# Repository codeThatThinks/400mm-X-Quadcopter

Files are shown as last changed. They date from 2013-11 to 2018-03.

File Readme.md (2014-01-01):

## Quadcopter

Drawings, Schematics, Firmware for a quadcopter platform based on APM

## License

The MIT License (MIT)

Copyright (c) 2014 Ian Glen

Permission is hereby granted, free of charge, to any person obtaining a copy of this software and associated documentation files (the "Software"), to deal in the Software without restriction, including without limitation the rights to use, copy, modify, merge, publish, distribute, sublicense, and/or sell copies of the Software, and to permit persons to whom the Software is furnished to do so, subject to the following conditions:

The above copyright notice and this permission notice shall be included in all copies or substantial portions of the Software.

THE SOFTWARE IS PROVIDED "AS IS", WITHOUT WARRANTY OF ANY KIND, EXPRESS OR IMPLIED, INCLUDING BUT NOT LIMITED TO THE WARRANTIES OF MERCHANTABILITY, FITNESS FOR A PARTICULAR PURPOSE AND NONINFRINGEMENT. IN NO EVENT SHALL THE AUTHORS OR COPYRIGHT HOLDERS BE LIABLE FOR ANY CLAIM, DAMAGES OR OTHER LIABILITY, WHETHER IN AN ACTION OF CONTRACT, TORT OR OTHERWISE, ARISING FROM, OUT OF OR IN CONNECTION WITH THE SOFTWARE OR THE USE OR OTHER DEALINGS IN THE SOFTWARE.

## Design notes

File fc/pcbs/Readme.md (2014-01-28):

## Control Board PCB

Control Board

An APM-compatible quadcopter autopilot board. Features an ATSAM4E16C ARM microcontroller, nRF24L01+ RF module, 10DOF IMU module, microSD card, 3.3v switching regulator, 3 SPI, 1 CAN, 1 UART, external navigation lights, an external temperature sensor, and 12 general purpose IO pins.

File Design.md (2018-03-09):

## Design
### Control Board
- APM-based board

- ATSAM3U2C-AU 32-bit Atmel ARM microcontroller
    - external crystal for clocking
    - firmware based on APM, FreeRTOS, ROS, or MultiWii
    - SRAM: run time data (APM: 8k)
    - Flash: firmware (APM: 256k)
    - EEPROM: configuration read from sd card (APM: 4k)
    - SPI (APM: 5)
    - I2C (APM: 1)
    - UART (APM: 4)
    - PWM (APM: 15)
    - external bus interface, for extending memory (APM: no)
    - APM: $17

- microSD card
    - external APM modules
    - configuration
    - data logger

- arming buzzer

- power
    - on/off switch
    - usb connector for external power
    - battery connector
    - connectors for 3.3v rail
    
    - switching power supply, 3.3v
        - provides 3v rail
        - powers all control electronics

    - battery voltage sensor through ADC
    - temp header for battery temp sensor
    - 20V resettable fuse

- connections
    - I2C (2)
    - SPI (1)
    - various ISPs/JTAGs/serials
    - misc I/O pins (analog, digital, PWM)

    - 4x 6-pin right-angle arm headers
        - ESC power (2 pins)
        - misc power (1 pin)
        - ground (1 pin)
        - empty (2 pin)

- LEDs
    - blue power LED
    - red/green arming status LED

    - nav LEDs:
        - 4x high power white strobe LEDs on rotor tips
        - green nav LED on front right rotor
        - red nav LED on front left rotor
        - 2x red strobe LEDs on bottom front and top back

### IMU
- connects via I2C to control board

- 9-axis board
    - gyro
    - accelrometer
    - altimeter/barometer/pressure sensor
    - sensor fusion

### RF
- nRF24L01+?
- full duplex RF
- Serial PPM

### Motors, Propellers, ESCs
- Turnigy D2830-11 1000kv motors
- APC 8x4 propellers
- Turnigy Multistar 30A ESCs (OPTO)
    - no BEC
    - reflash with SimonK firmware with Arduino

### Frame
- 15 7/16" x 1/4" extruded plastic tube

### Battery

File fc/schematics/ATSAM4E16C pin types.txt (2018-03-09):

Power Supplies
5 - VDDIN
19 - VDDIO
28 - VDDIO
68 - VDDIO
93 - VDDIO

4 - VDDOUT
18 - VDDCORE
22 - VDDCORE
86 - VDDCORE
96 - VDDPLL

3 - GND
6 - GND
7 - GND
8 - GND
10 - GND
29 - GND
67 - GND

Clocks, Oscillators, PLLs
24 - XIN32
25 - XOUT32
99 - XIN
98 - XOUT

81 - PCK0
100 - PCK0
16 - PCK1
21 - PCK1
15 - PCK2
20 - PCK2
83 - PCK2

real-time clock
12 - RTCOUT0
11 - RTCOUT1

SWD/JTAG
57 - TMS/SWDIO
63 - TCK/SWCLK
73 - JTAGSEL
74 - TDI
77 - TDO/TRACESWO

Flash
61 - ERASE

Reset/Test
58 - NRST
60 - TST

UART
46 - UTXD0
54 - URXD0
81 - UTXD1
52 - URXD1

PIOA
72 - PA0
70 - PA1
66 - PA2
64 - PA3
55 - PA4
52 - PA5
81 - PA6
24 - PA7
25 - PA8
54 - PA9
46 - PA10
44 - PA11
48 - PA12
27 - PA13
34 - PA14
33 - PA15
30 - PA16
16 - PA17
15 - PA18
14 - PA19
13 - PA20
21 - PA21
26 - PA22
31 - PA23
38 - PA24
40 - PA25
42 - PA26
50 - PA27
79 - PA28
90 - PA29
82 - PA30
83 - PA31

PIOB
12 - PB0
11 - PB1
17 - PB2
20 - PB3
74 - PB4
77 - PB5
57 - PB6
63 - PB7
98 - PB8
99 - PB9
94 - PB10
95 - PB11
61 - PB12
100 - PB13
97 - PB14

PIOD
1 - PD0
92 - PD1
91 - PD2
89 - PD3
88 - PD4
87 - PD5
85 - PD6
84 - PD7
80 - PD8
78 - PD9
71 - PD10
69 - PD11
65 - PD12
62 - PD13
59 - PD14
75 - PD15
56 - PD16
53 - PD17
49 - PD18
47 - PD19
45 - PD20
43 - PD21
41 - PD22
39 - PD23
37 - PD24
35 - PD25
36 - PD26
32 - PD27
51 - PD28
76 - PD29
23 - PD30
2 - PD31

PIO Parallel Capture Mode
31 - PIODCCLK
33 - PIODCEN1
30 - PIODCEN2
38 - PIODC0
40 - PIODC1
42 - PIODC2
50 - PIODC3
79 - PIODC4
90 - PIODC5
82 - PIODC6
83 - PIODC7

SD Card
90 - MCCK
79 - MCCDA
82 - MCDA0
83 - MCDA1
42 - MCDA2
50 - MCDA3

USART
100 - SCK0
11 - TXD0
12 - RXD0
20 - RTS0
17 - CTS0

31 - SCK1
26 - TXD1
21 - RXD1
38 - RTS1
40 - CTS1
50 - DTR1
79 - DSR1
42 - DCD1
90 - RI1

Timer/Counter
72 - TIOA0
70 - TIOB0
55 - TCLK0
33 - TIOA1
30 - TIOB1
79 - TCLK1
42 - TIOA2
50 - TIOB2
90 - TCLK2

SPI
48 - MISO
27 - MOSI
34 - SPCK

44 - NPCS0
54 - NPCS1
83 - NPCS1
97 - NPCS1
17 - NPCS2
46 - NPCS2
82 - NPCS2
26 - NPCS3
52 - NPCS3
64 - NPCS3

I2C
64 - TWD0
55 - TWCK0
74 - TWD1
77 - TWCK1

Analog
9 - ADVREF

12-bit AFE
25 - AFE0_ADTRG
16 - AFE0_AD0
15 - AFE0_AD1
14 - AFE0_AD2
13 - AFE0_AD3
12 - AFE0_AD4
11 - AFE0_AD5
17 - AFE1_AD0
20 - AFE1_AD1
21 - AFE1_AD2
26 - AFE1_AD3

12-bit DAC
66 - DATRG
100 - DAC0
97 - DAC1

FFPI
55 - PGMN0
52 - PGMN1
81 - PGMN2
24 - PGMN3

25 - PGMD0
54 - PGMD1
46 - PGMD2
44 - PGMD3
48 - PGMD4
27 - PGMD5
34 - PGMD6
33 - PGMD7
30 - PGMD8
16 - PGMD9
15 - PGMD10
14 - PGMD11
13 - PGMD12
21 - PGMD13
26 - PGMD14
31 - PGMD15

70 - PGMRDY
64 - PGMNVALID
66 - PGMNOE

PWM
54 - PWMFI0

12 - PWMH0
31 - PWMH0
44 - PWMH0
45 - PWMH0
72 - PWMH0
14 - PWML0
37 - PWML0
77 - PWML0

11 - PWMH1
38 - PWMH1
43 - PWMH1
48 - PWMH1
70 - PWMH1
13 - PWML1
35 - PWML1
61 - PWML1

27 - PWMH2
40 - PWMH2
41 - PWMH2
66 - PWMH2
74 - PWMH2
30 - PWML2
36 - PWML2
82 - PWML2
100 - PWML2

16 - PWMH3
24 - PWMH3
34 - PWMH3
39 - PWMH3
97 - PWMH3
32 - PWML3
33 - PWML3

Ethernet
1 - GREFCK
1 - GTXCK
59 - GRXCK
92 - GTXEN
91 - GTX0
89 - GTX1
75 - GTX2
56 - GTX3
53 - GTXER
88 - GRXDV
87 - GRX0
85 - GRX1
69 - GRX2
65 - GRX3
84 - GRXER
71 - GCRS
88 - GCRSDV
62 - GCOL
80 - GMDC
78 - GMDIO

CAN
17 - CANTX0
20 - CANRX0

USB
94 - DDM
95 - DDP

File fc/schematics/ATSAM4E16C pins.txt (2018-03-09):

1 PD0
2 PD31
3 GND
4 VDDOUT
5 VDDIN
6 GND
7 GND
8 GND
9 ADVREF
10 GND
11 PB1
12 PB0
13 PA20/PGMD12
14 PA19/PGMD11
15 PA18/PGMD10
16 PA17/PGMD9
17 PB2
18 VDDCORE
19 VDDIO
20 PB3
21 PA21/PGMD13
22 VDDCORE
23 PD30
24 PA7/PGMN3
25 PA8/PGMD0
26 PA22/PGMD14
27 PA13/PGMD5
28 VDDIO
29 GND
30 PA16/PGMD8
31 PA23/PGMD15
32 PD27
33 PA15/PGMD7
34 PA14/PGMD6
35 PD25
36 PD26
37 PD24
38 PA24
39 PD23
40 PA25
41 PD22
42 PA26
43 PD21
44 PA11/PGMD3
45 PD20
46 PA10/PGMD2
47 PD19
48 PA12/PGMD4
49 PD18
50 PA27
51 PD28
52 PA5/PGMN1
53 PD17
54 PA9/PGMD1
55 PA4/PGMN0
56 PD16
57 PB6
58 NRST
59 PD14
60 TST
61 PB12
62 PD13
63 PB7
64 PA3/PGMNVALID
65 PD12
66 PA2/PGMNOE
67 GND
68 VDDIO
69 PD11
70 PA1/PGMRDY
71 PD10
72 PA0
73 JTAGSEL
74 PB4
75 PD15
76 PD29
77 PB5
78 PD9
79 PA28
80 PD8
81 PA6/PGMN2
82 PA30
83 PA31
84 PD7
85 PD6
86 VDDCORE
87 PD5
88 PD4
89 PD3
90 PA29
91 PD2
92 PD1
93 VDDIO
94 PB10
95 PB11
96 VDDPLL
97 PB14
98 PB8
99 PB9
100 PB13

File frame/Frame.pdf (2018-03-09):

## PROJECT TITLE

MONTH, DD YYYY

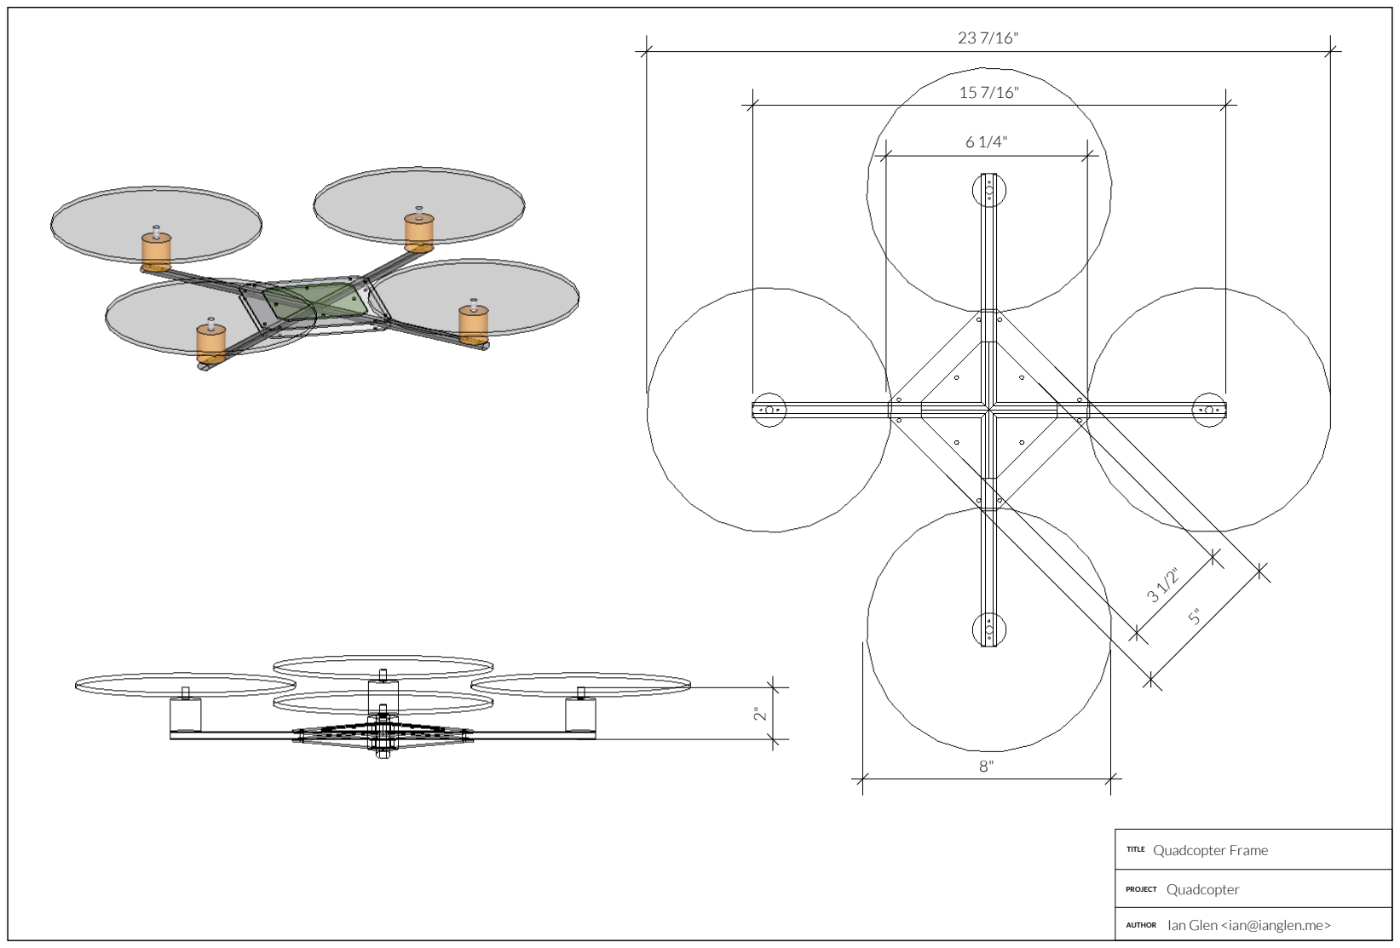
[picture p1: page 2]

TITLE

PROJECT

AUTHOR

Quadcopter Frame

Quadcopter

Ian Glen <ian@ianglen.me>

23 7/16"

15 7/16"

3 1/2"

5"

8"

6 1/4"

2"

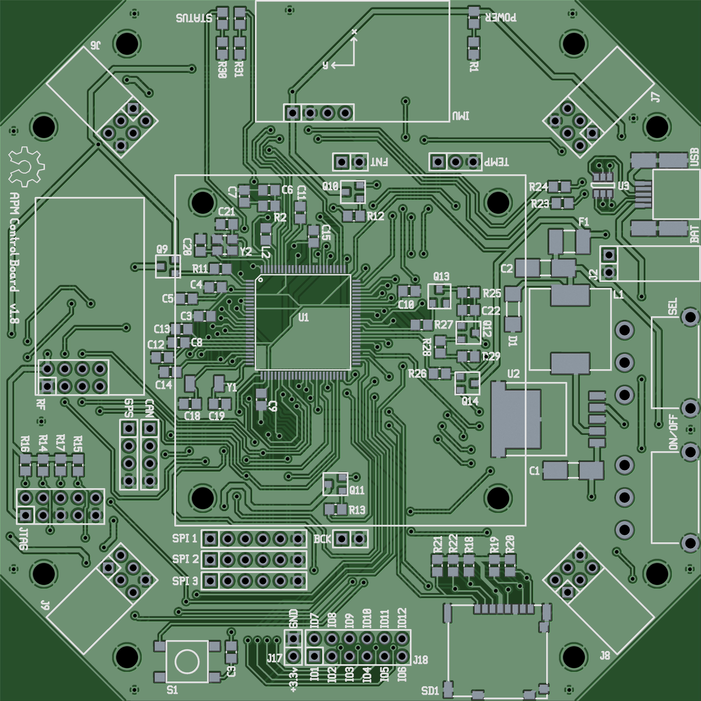
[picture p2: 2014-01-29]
fc/pcbs/Control Board.png

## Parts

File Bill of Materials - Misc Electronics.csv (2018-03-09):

Quantity | Item | URL | Unit Price | Price
4 | 1300mcd white led | http://www.mouser.com/ProductDetail/Kingbright/AA2214VR4D1S-C1/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 | $1.00 | $4.00
4 | 1R 0805 resistor

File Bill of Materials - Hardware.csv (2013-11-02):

Quantity | Item | URL | Cost
4 | Turnigy D2830-11 1000kv motor | http://www.hobbyking.com/hobbyking/store/__28115__D2830_11_1000kv_Brushless_Motor_USA_Warehouse_.html | $39.88
4 | Turnigy Multistar 30A ESC (OPTO) | http://www.hobbyking.com/hobbyking/store/__27776__Turnigy_Multistar_30_Amp_Multi_rotor_Brushless_ESC_2_4S_OPTO_.html | $44.60
1 | APC 8x4 CW propeller (2 pack) | http://hobbyking.com/hobbyking/store/__22971__APC_Style_Propeller_8x4R_Right_Hand_Rotation_2pc_.html | $1.79
1 | APC 8x4 CCW propeller (2 pack) | http://hobbyking.com/hobbyking/store/__22425__APC_Style_Propeller_8x4_2_pc_.html | $2.02
1 | Zippy 4000mAh 3S 25C Lipo | http://hobbyking.com/hobbyking/store/__21360__ZIPPY_Compact_4000mAh_3S_25C_Lipo_Pack.html | $22.30
 |  |  | Total: $110.59

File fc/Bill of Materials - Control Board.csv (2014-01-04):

Quantity | References | Item | URL | Unit Price | Price
ICs
1 | U1 | ATSAM4E16CA-AU | http://www.digikey.com/short/qrd10 | $11.09 | $11.09
1 | U2 | LM2596S-3.3/NOPB | http://www.digikey.com/short/qr0cr | $4.54 | $4.54
1 | U3 | IP4234CZ6-125 | http://www.digikey.com/short/qr077 | $0.46 | $0.46
Inductors
1 | L1 | 100uH inductor | http://www.digikey.com/short/qr07p | $4.42 | $4.42
1 | L2 | 10uH 0805 inductor | http://www.digikey.com/short/qr07r | $0.08 | $0.08
Capacitors
1 | C1 | 100uF low ESR capacitor | http://www.digikey.com/short/qr070 | $1.49 | $1.49
1 | C2 | 470uF low ESR capacitor | http://www.digikey.com/short/qr0tq | $2.46 | $2.46
2 | C3 C12 | 10uF 0805 capacitor | http://www.digikey.com/short/qr0t4 | $0.16 | $0.32
1 | C4 | 2.2uF 0805 capacitor | http://www.digikey.com/short/qr0tf | $0.12 | $0.12
11 | C5-C6 C8-C11 C13-17 | 100nF 0805 capacitor | http://www.digikey.com/short/qr0t1 | $0.03 | $0.34
1 | C7 | 4.7uF 0805 capacitor | http://www.digikey.com/short/qr034 | $0.10 | $0.10
2 | C18-C19 | 22pF 0805 capacitor | http://www.digikey.com/short/qr035 | $0.10 | $0.20
2 | C20-C21 | 1pF 0805 capacitor | http://www.digikey.com/short/qr0q7 | $0.11 | $0.22
1 | C22 | 100pF 0805 capacitor | http://www.digikey.com/short/qr0qp | $0.10 | $0.10
Diodes
1 | D1 | SK32 3A schotty diode | http://www.digikey.com/short/qr0qb | $0.57 | $0.57
1 | LED_PWR | 0805 blue led | http://www.digikey.com/short/qr0q0 | $0.51 | $0.51
1 | LED_ARED | 0805 red led | http://www.digikey.com/short/qr083 | $0.19 | $0.19
1 | LED_AGRN | 0805 green led | http://www.digikey.com/short/qr08m | $0.23 | $0.23
Resistors
2 | R1-R2 | 1R 0805 resistor | http://www.digikey.com/short/qr08f | $0.04 | $0.08
11 | R3-R13 | 300K 0805 resistor | http://www.digikey.com/short/qr0jc | $0.02 | $0.21
5 | R14-R17 R25 | 100K 0805 resistor | http://www.digikey.com/short/qr0jp | $0.04 | $0.20
5 | R18-R22 | 47K 0805 resistor | http://www.digikey.com/short/qr0j2 | $0.04 | $0.20
2 | R23-R24 | 27R 0805 resistor | http://www.digikey.com/short/qr0j1 | $0.10 | $0.20
2 | R26-R27 | 2K 0805 resistor | http://www.digikey.com/short/qr0p2 | $0.04 | $0.08
1 | R28 | 680R 0805 resistor | http://www.digikey.com/short/qr0z8 | $0.04 | $0.04
1 | R29 | 270R 0805 resistor | http://www.digikey.com/short/qr0zh | $0.04 | $0.04
1 | R30 | 75R 0805 resistor | http://www.digikey.com/short/qr0zd | $0.04 | $0.04
1 | R31 | 60R4 0805 resistor | http://www.digikey.com/short/qr04t | $0.04 | $0.04
Transistors
11 | Q1-Q11 | PBMTA14-215 SOT23 | http://www.digikey.com/short/qr04r | $0.36 | $3.96
1 | Q12 | NTR0202PL SOT23 | http://www.digikey.com/short/qr0m3 | $0.52 | $0.52
2 | Q13-Q14 | BC817 SOT23 | http://www.digikey.com/short/qr0mr | $0.21 | $0.42
Switches
2 | PWR PWR_SEL | STDP 5A slide switch | http://www.digikey.com/short/qr0h4 | $2.93 | $5.86
Crystals
1 | Y1 | 32.768KHz crystal | http://www.digikey.com/short/qr0hn | $0.82 | $0.82
1 | Y2 | 12MHz crystal | http://www.digikey.com/short/qr09t | $0.90 | $0.90
Headers
1 | J1 | 2x5 male shrouded | http://www.digikey.com/short/qr09p | $0.26 | $0.26
1 | J2 | 1x2 male right-angle | http://www.digikey.com/short/qr09r | $0.52 | $0.52
1 | J3 | 2x4 female | http://www.digikey.com/short/qr09d | $0.84 | $0.84
33 | J4-J5 J10-J15 | 1x33 male breakaway | http://www.digikey.com/short/qr0b4 | $0.11 | $3.91
4 | J6-J9 | 2x3 male right-angle | http://www.digikey.com/short/qr0bf | $1.07 | $4.28
1 | J16 | 1x4 female | http://www.digikey.com/short/qr05t | $0.60 | $0.60
Misc
1 | F1 | Resettable PTC Fuse 3A | http://www.digikey.com/short/qr05d | $0.15 | $0.15
1 | USB1 | Mini USB AB socket | http://www.digikey.com/short/qr0rz | $2.92 | $2.92
1 | SD1 | Micro SD socket | http://www.digikey.com/short/qr0r9 | $1.84 | $1.84
 |  |  |  | Total: | $56.37

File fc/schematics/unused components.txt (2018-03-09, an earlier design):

unused components
===============================
C12 - 10uF 0805 capacitor
C16 - 100nF 0805 capacitor
C17 - 100nF 0805 capacitor

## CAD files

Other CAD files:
frame/quadcopter.stp
frame/Frame-hidden.skp
frame/Frame.skp

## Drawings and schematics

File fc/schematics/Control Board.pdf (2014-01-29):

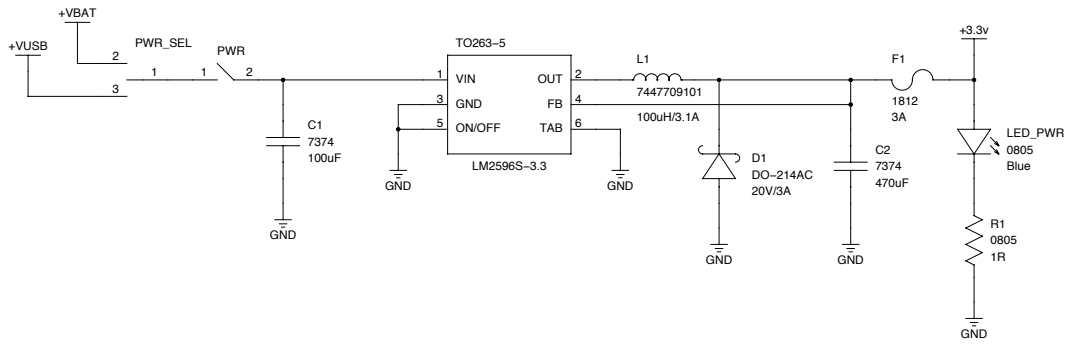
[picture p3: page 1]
DRAWN BY:; PROJECT:; TITLE:; Power; ON/OFF; GND; VIN; 6 TAB; 2 OUT; +VBAT; +VUSB; PWR_SEL; PWR; LED_PWR; Blue

Quadcopter Control Board

Ian Glen <ian@ianglen.me>

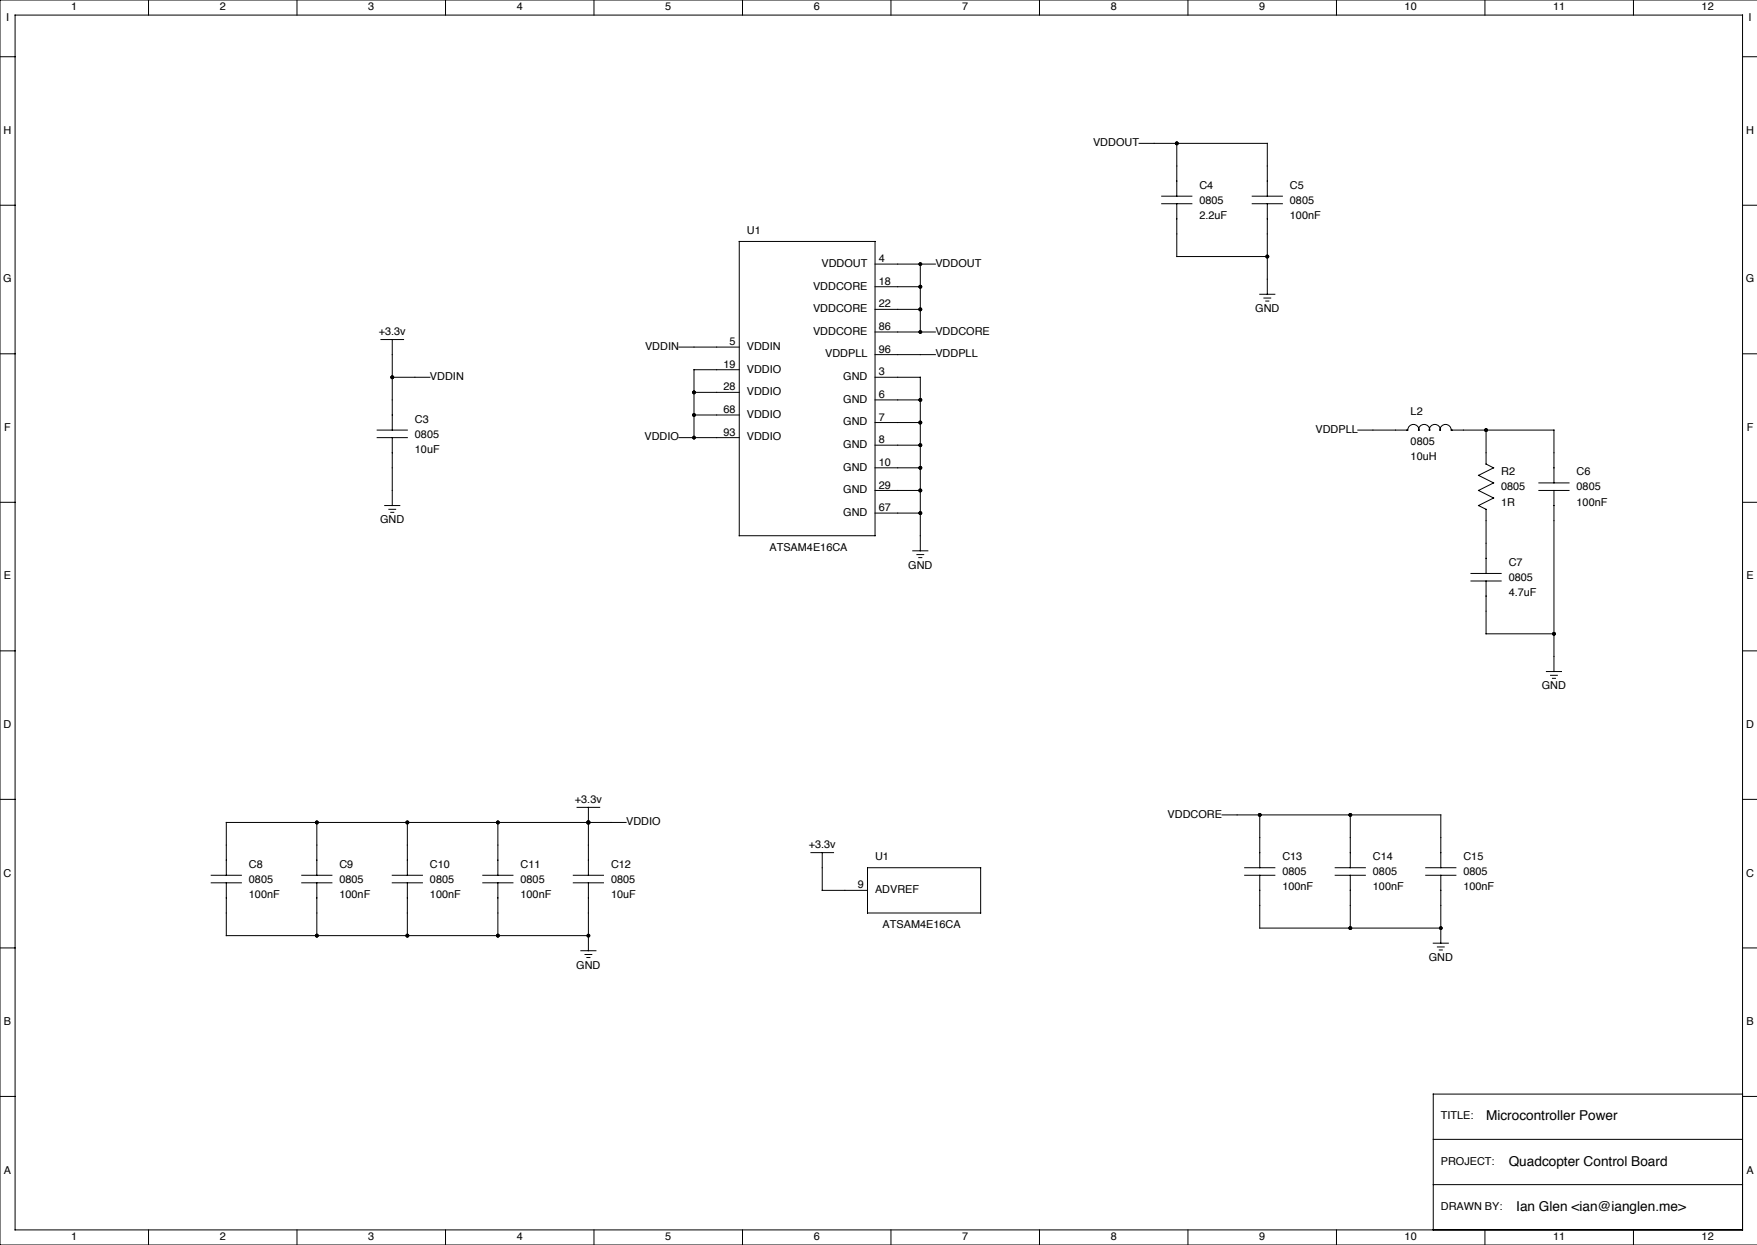
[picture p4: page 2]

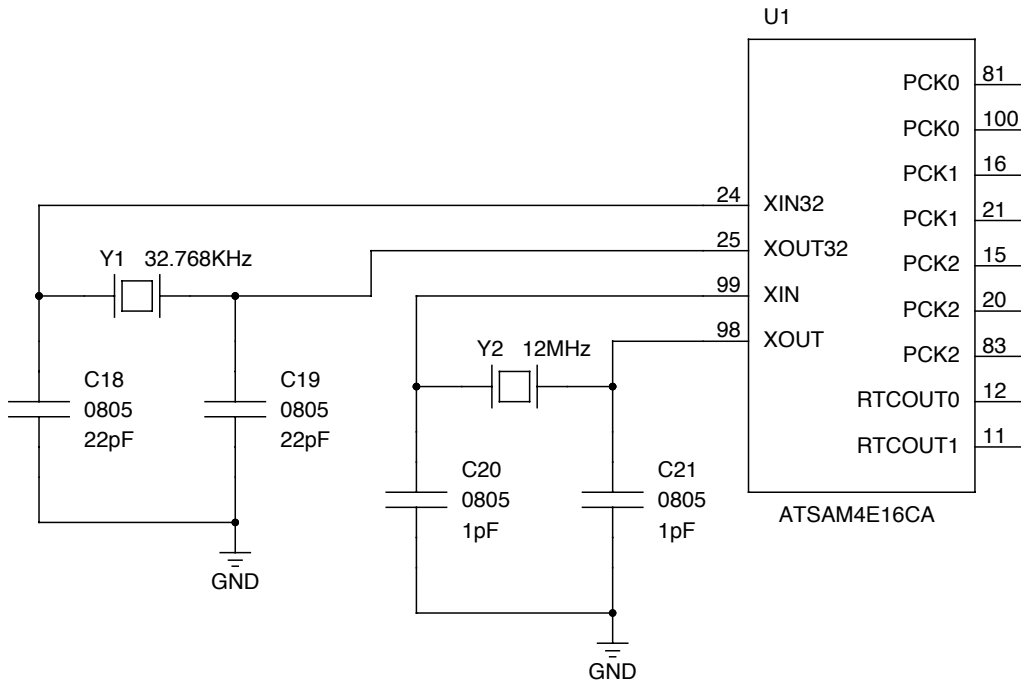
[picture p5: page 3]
TITLE:; Microcontroller Oscillators; Y2 12MHz; Y1 32.768KHz; GND; XOUT; XIN; XOUT32; XIN32; 11 RTCOUT1; 12 RTCOUT0; 83 PCK2; 20 PCK2; 15 PCK2; 21 PCK1; 16 PCK1; 100 PCK0; 81 PCK0; ATSAM4E16CA

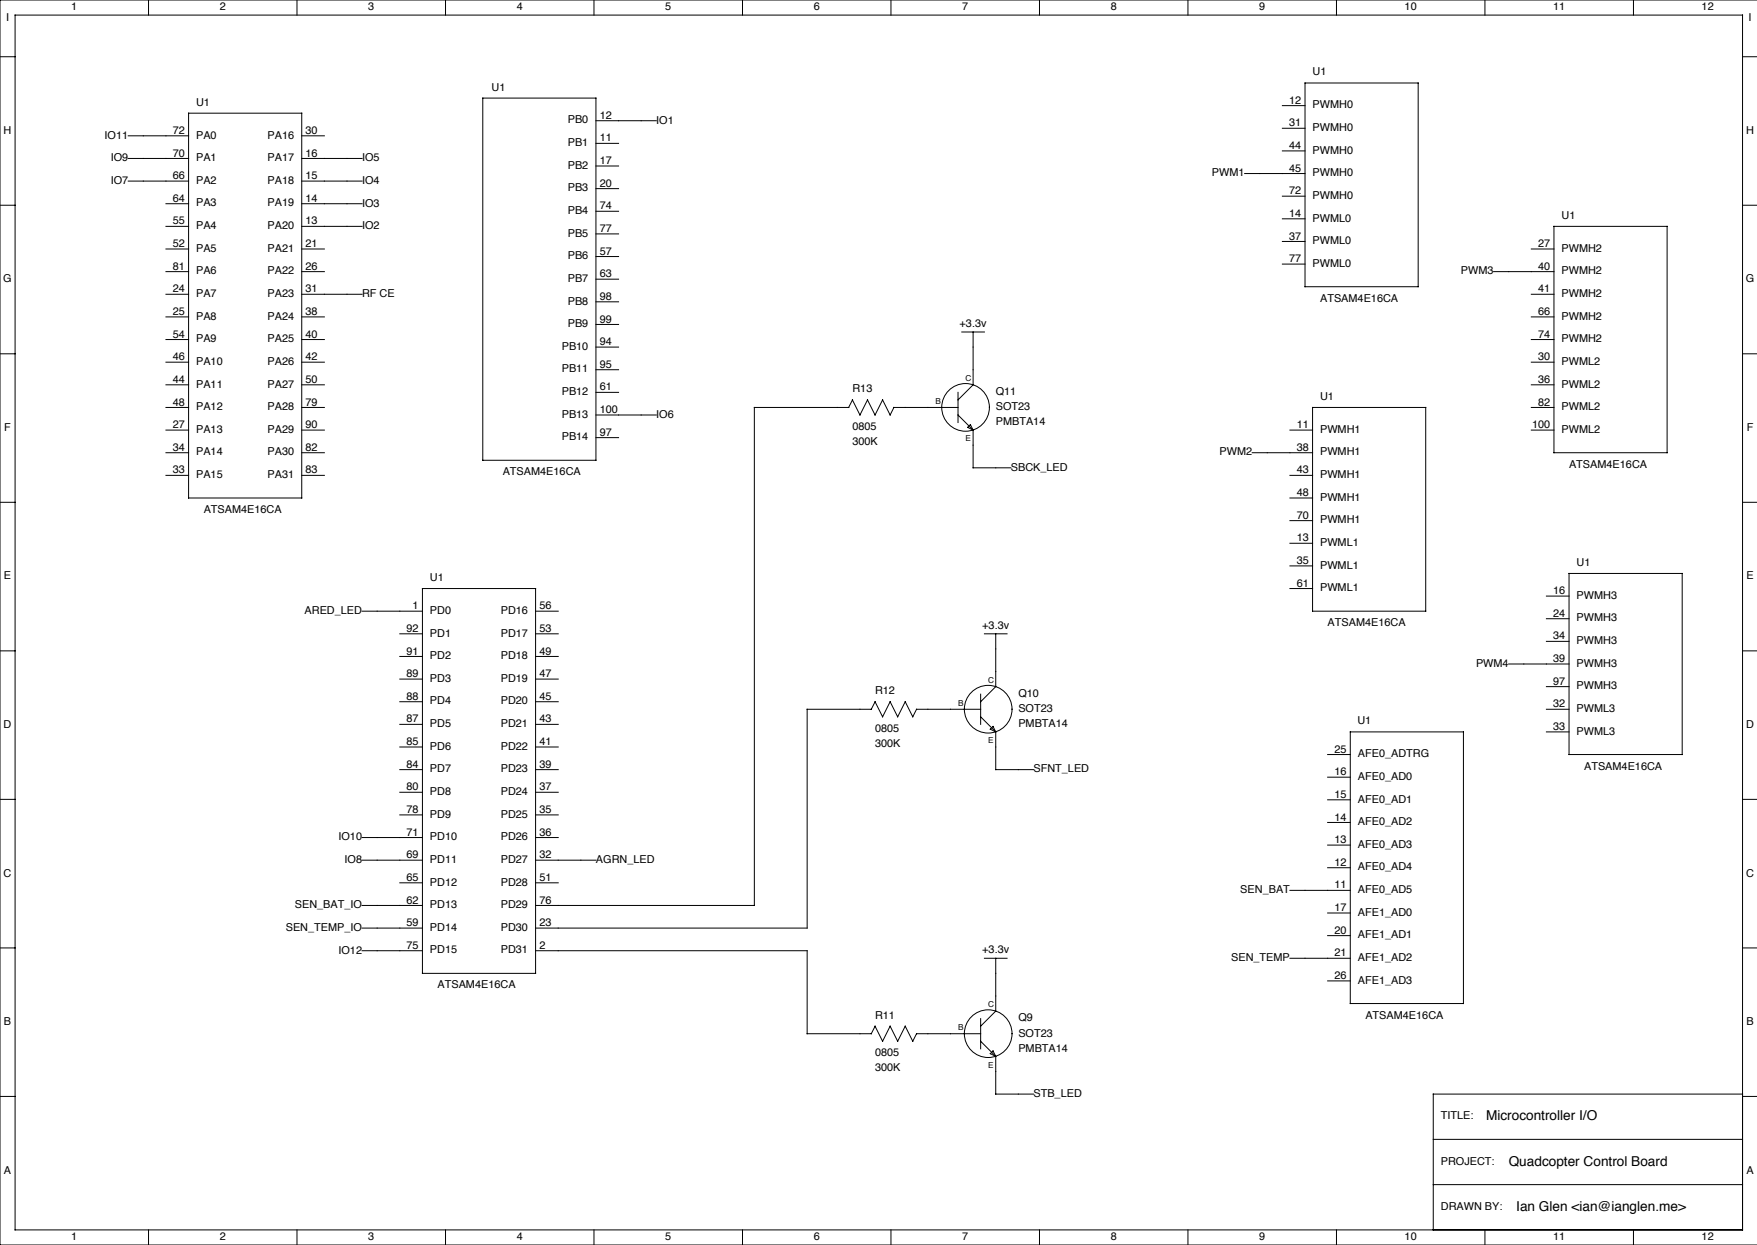
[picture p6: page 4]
TITLE:; ABCDEFGH; Microcontroller I/O; SFNT_LED; SBCK_LED; AGRN_LED; ARED_LED; STB_LED; PWML0; PWMH0; ATSAM4E16CA; PWML1; PWMH1; PWML2; PWMH2; PWML3; PWMH3; PWM1; PWM2; PWM3; PWM4; SEN_TEMP_IO; SEN_BAT_IO; Q9 SOT23 PMBTA14; Q10 SOT23 PMBTA14; Q11 SOT23 PMBTA14; AFE1_AD3; AFE1_AD2; AFE1_AD1; AFE1_AD0; AFE0_AD5; AFE0_AD4; AFE0_AD3; AFE0_AD2; AFE0_AD1; AFE0_AD0; AFE0_ADTRG; SEN_BAT; SEN_TEMP

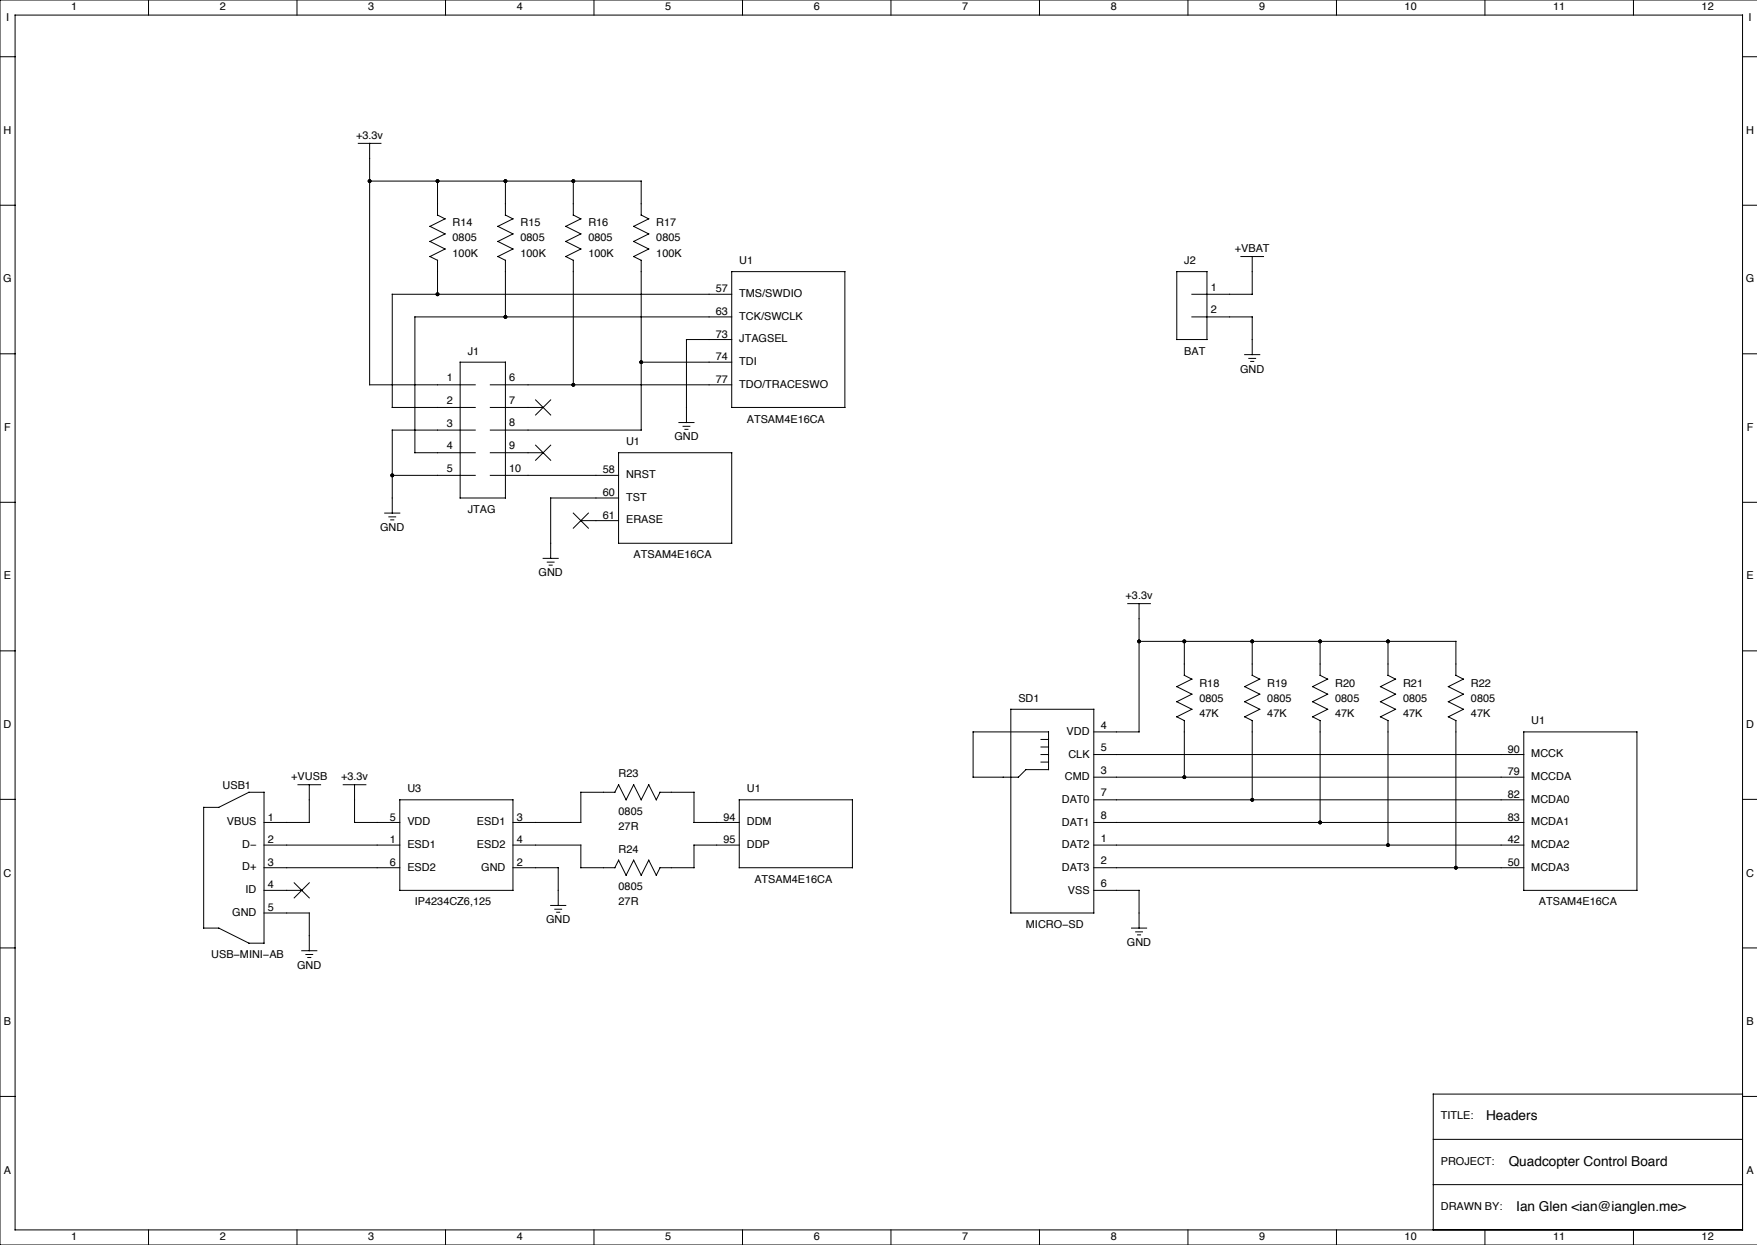
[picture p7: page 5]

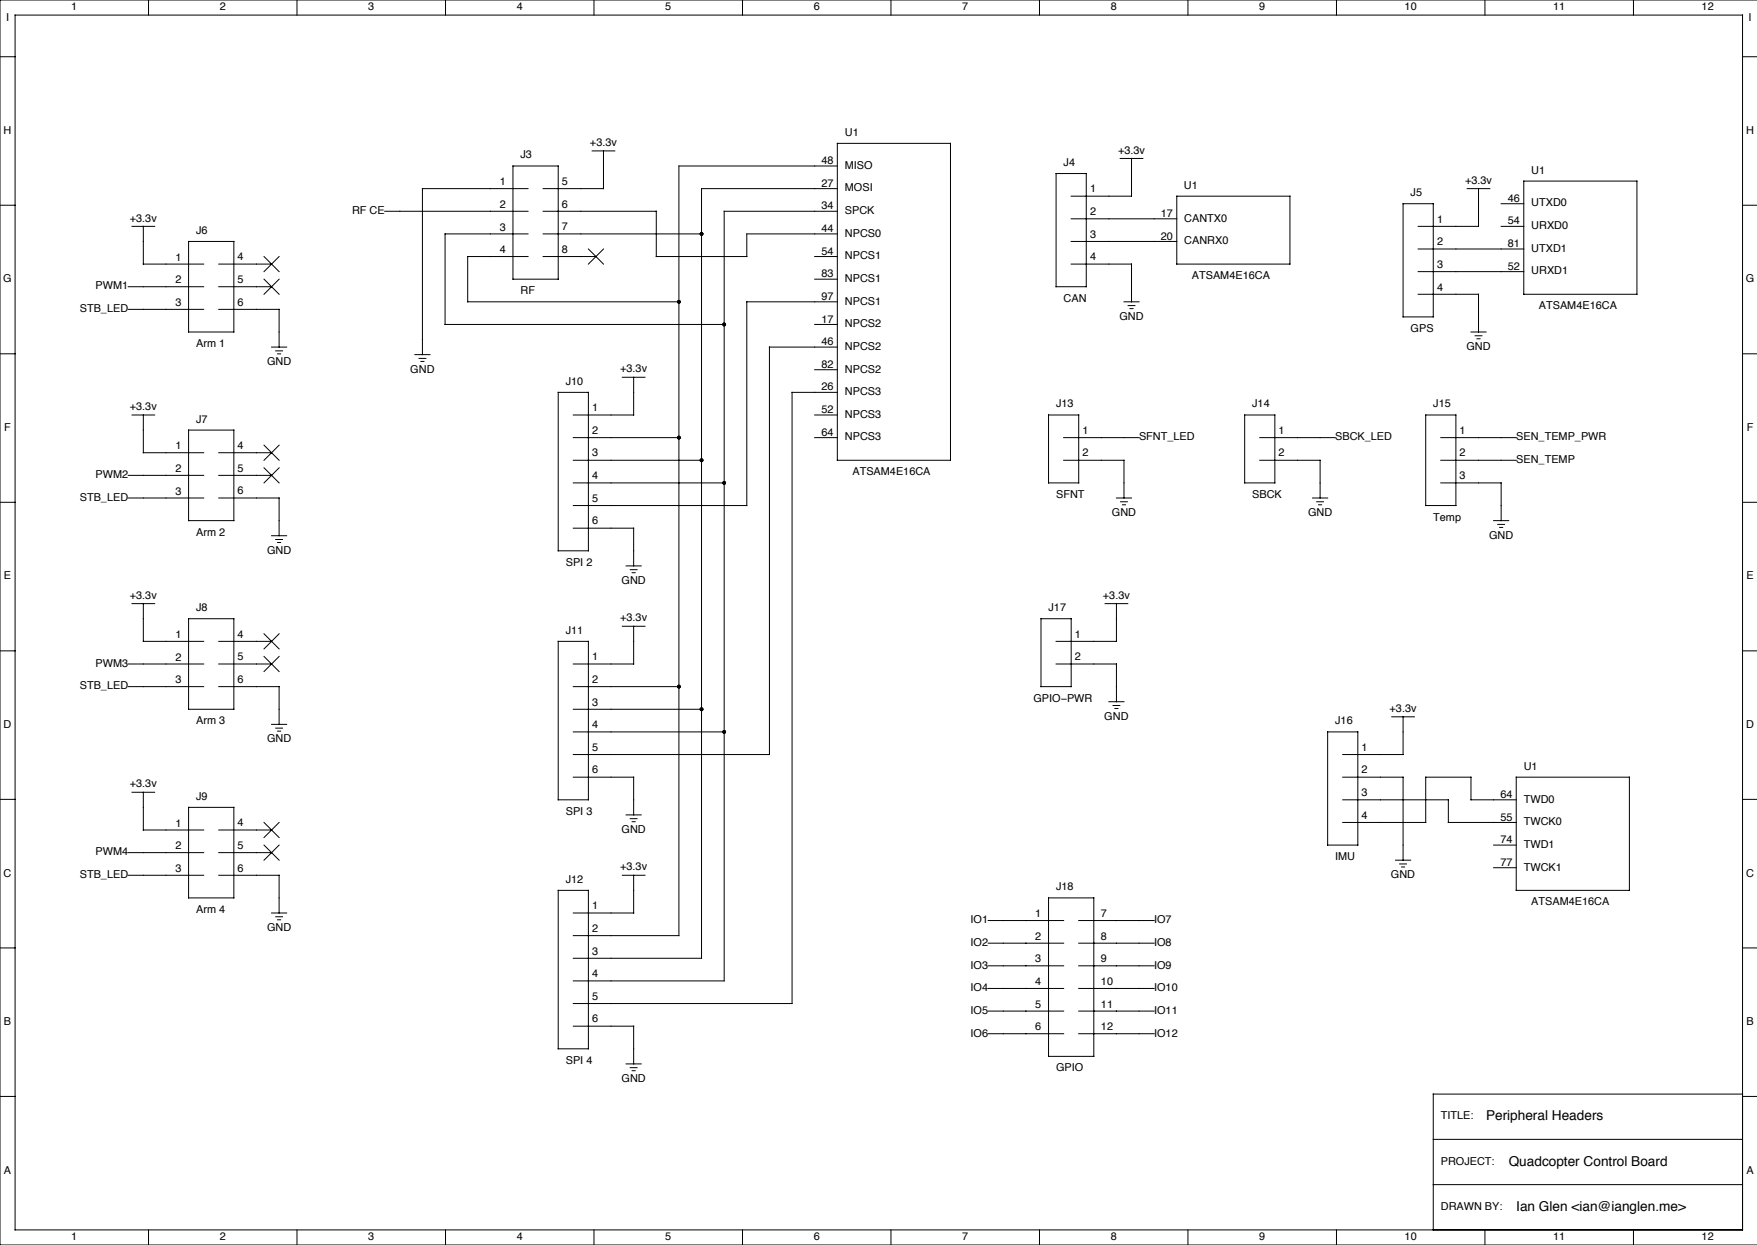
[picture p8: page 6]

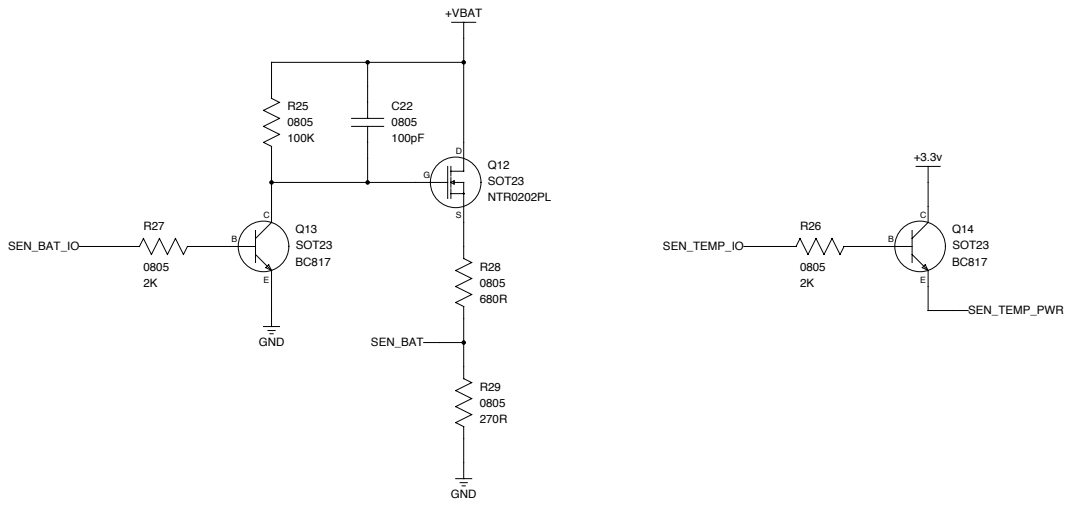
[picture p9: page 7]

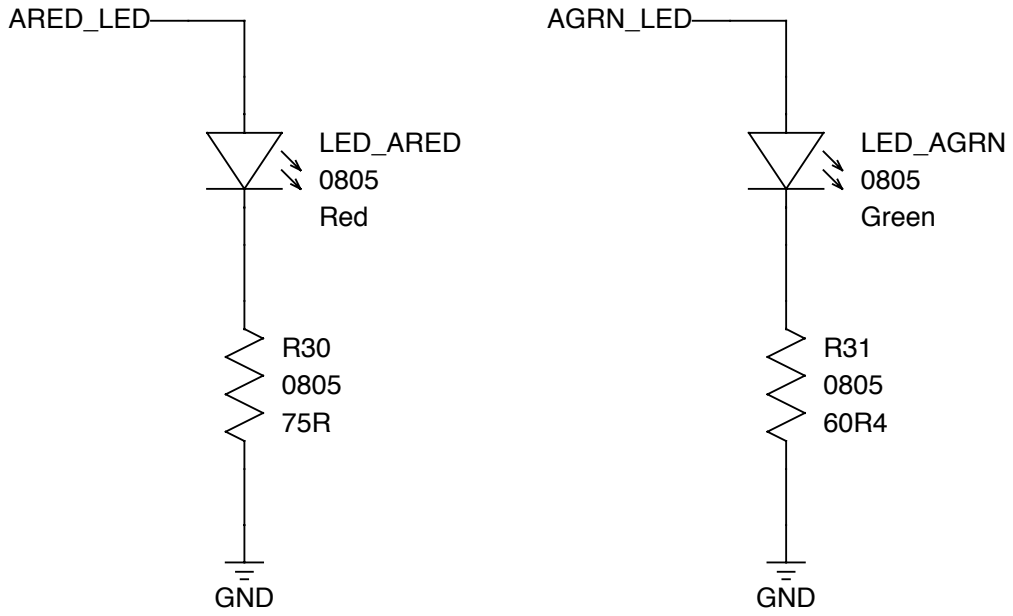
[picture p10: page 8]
TITLE:; LEDs; LED_ARED 0805 Red; LED_AGRN 0805 Green; ARED_LED; AGRN_LED; GND

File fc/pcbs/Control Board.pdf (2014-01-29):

# /root/Quadcopter/pcbs/Control Board.pcb

# 1. Table of Contents (This Page) Created on Wed Jan 29 14:36:37 2014

# 2. top 3. bottom 4. plated-drill 5. componentmask 6. soldermask 7. topsilk 8. bottomsilk 9. toppaste 10. topassembly 11. bottomassembly 12. fab

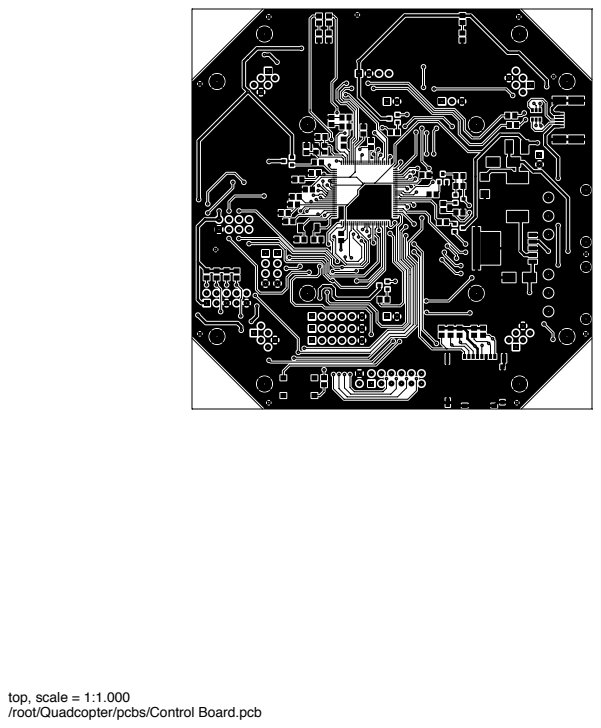
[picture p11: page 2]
top, scale = 1:1.000

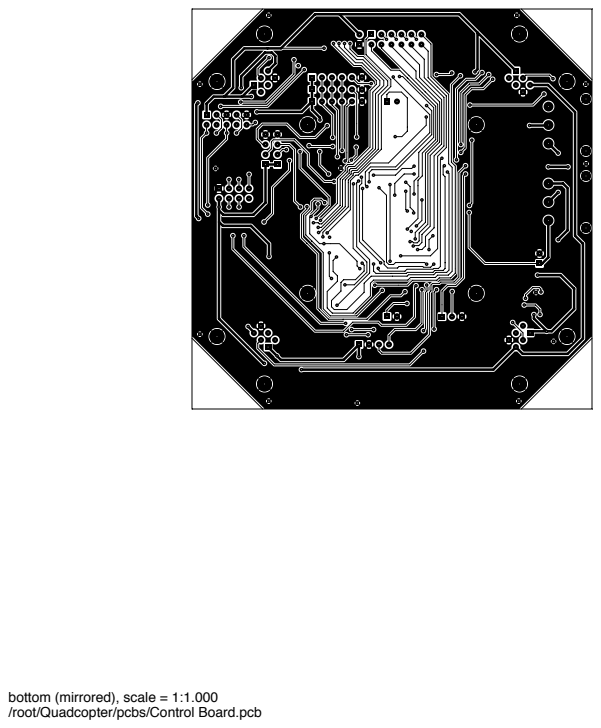
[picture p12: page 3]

bottom (mirrored), scale = 1:1.000

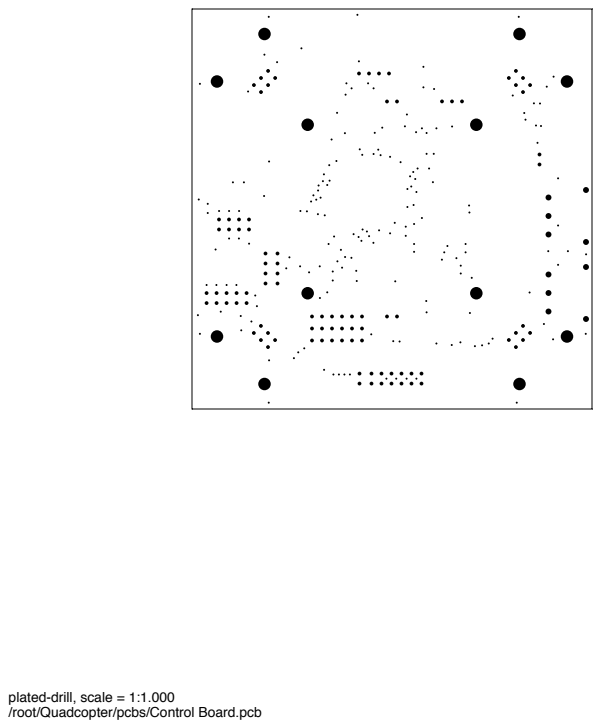
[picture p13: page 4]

plated-drill, scale = 1:1.000

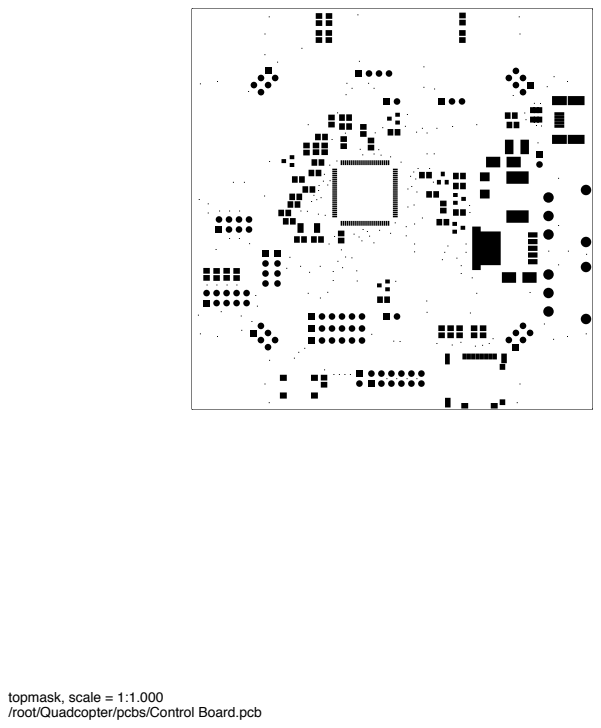
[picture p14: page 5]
topmask, scale = 1:1.000


bottommask (mirrored), scale = 1:1.000

topsilk, scale = 1:1.000

bottomsilk (mirrored), scale = 1:1.000

toppaste, scale = 1:1.000

topassembly, scale = 1:1.000


bottomassembly (mirrored), scale = 1:1.000

fab, scale = 1:1.000

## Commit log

2013-10-22 Added microcontroller list
    [Atmel ARM Microcontrollers.csv]
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2013-10-22 Added bill of materials
    [Bill of Materials.csv]
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2013-10-23 Added motors and props, changed around columns
    [Bill of Materials.csv]
2013-10-23 Updated motor, propeller, and ESC design
2013-10-24 Added ESCs
    [Bill of Materials.csv]
2013-10-24 Split bill of materials into individual files
    [Bill of Materials - Control Board.csv, Bill of Materials - Hardware.csv]
2013-10-24 Added APM and FLC to useful stuff
    [APM 2.6 PCB.brd, APM 2.6 Schematic.sch]
2013-10-24 Replaced APM Eagle schematic with png
    [APM 2.6 PCB.brd, APM 2.6 Schematic.sch]
2013-10-29 Updated ATSAM3C2U schematic symbols
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2013-10-29 Preliminary power schematic
    [Control Board - Power.sch]
2013-10-29 Added LM2596S-3.3 symbol for power schematic
2013-10-29 Preliminary mcu power schematic
    [Control Board - Microcontroller Power.sch]
2013-10-30 Preliminary header schematic
    [Control Board - Headers.sch]
2013-10-30 Preliminary microSD schematic
    [Control Board - MicroSD Card.sch]
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2013-10-30 Split header schematic into two files
    [Control Board - Headers.sch, Control Board - Peripheral Headers.sch]
2013-10-30 Preliminary LED schematic
    [Control Board - LEDs.sch]
2013-10-30 Added sensors schematic
    [Control Board - Sensors.sch]
2013-11-01 Added ADC power
    [Control Board - Microcontroller Power.sch]
2013-11-01 Added temperature header
    [Control Board - Peripheral Headers.sch]
2013-11-01 Preliminary microcontroller io schematic
    [Control Board - Microcontroller IO.sch]
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2013-11-01 Added programming and erase push buttons
    [Control Board - Power.sch]
2013-11-01 Added battery voltage sensor
    [Control Board - Sensors.sch]
2013-11-02 Added battery
    [Bill of Materials - Hardware.csv]
2013-11-03 Renumbered references
    [Control Board - Headers.sch, Control Board - Microcontroller IO.sch, Control Board - Microcontroller Power.sch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]
2013-11-03 Added pull up resistors
    [Control Board - MicroSD Card.sch]
2013-11-04 Updated resistor labels
    [Control Board - MicroSD Card.sch]
2013-11-04 Added footprints, updated nets
    [Control Board - MicroSD Card.sch]
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2013-11-06 Added mosfet, updated footprints and nets
    [Control Board - Sensors.sch]
2013-11-06 Updated footprints and nets
    [Control Board - Headers.sch]
2013-11-07 Added net for NRSTB pin
    [Control Board - Power.sch]
2013-11-07 Updated nets and GPIO header
    [Control Board - Microcontroller IO.sch]
2013-11-07 Updated references
    [Control Board - Sensors.sch]
2013-11-07 Updated LED references
    [Control Board - LEDs.sch]
2013-11-07 Updated LED reference
    [Control Board - Power.sch]
2013-11-07 Added oscillators schematic
    [Control Board - Oscillators.sch]
2013-11-07 Updated bom to match schematics
    [Bill of Materials - Control Board.csv]
2013-11-08 Updated component values, added capacitors to prgm and erase buttons
    [Control Board - Power.sch]
2013-11-08 Added footprint to both inductors
    [Control Board - Microcontroller Power.sch]
2013-11-08 Substituted 0.8 ohm resistor for 1 ohm resistor
    [Control Board - Power.sch]
2013-11-09 Rerouted LEDs through transistor array
    [Control Board - LEDs.sch, Control Board - Microcontroller IO.sch]
2013-11-09 Updated nets
    [Control Board - Microcontroller IO.sch]
2013-11-09 Added strobe front/back LED headers
    [Control Board - Peripheral Headers.sch]
2013-11-09 Updated footprints
    [Control Board - Peripheral Headers.sch]
2013-11-09 Moved battery ADC transistor to array
    [Control Board - Microcontroller IO.sch, Control Board - Sensors.sch]
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2013-11-10 Adjusted capacitors to match crystal capacitance
    [Control Board - Oscillators.sch]
2013-11-10 Made changes for noisy environments
    [Control Board - Power.sch]
2013-11-10 Unused 10-bit ADC is tied to ground
    [Control Board - Sensors.sch]
2013-11-10 Fixed weird placement of input capacitor
    [Control Board - Power.sch]
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2014-01-03 Added fuse, IP4234CZ6,125, and 4x2 header symbols. Replaced usb-mini-b with usb-mini-ab connector symbol
2014-01-03 Updated schematics for new processor and peripheral-specific headers
    [Control Board - Headers.sch, Control Board - LEDs.sch, Control Board - MicroSD Card.sch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]
2014-01-03 Updated crystal capacitance
    [Control Board - Oscillators.sch]
2014-01-04 Updated control board bom
    [Bill of Materials - Control Board.csv]
2014-01-04 Updated transistors and their resistor values, added GPIO header, LED resistor values, and renumbered all component references
    [Control Board - Headers.sch, Control Board - LEDs.sch, Control Board - Microcontroller IO.sch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]
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2014-01-04 Fixed csv formatting errors
    [Bill of Materials - Control Board.csv]
2014-01-04 Updated footprints, nets, and fixed typos
    [Control Board - Headers.sch, Control Board - LEDs.sch, Control Board - Microcontroller IO.sch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]
2014-01-07 Updated footprints, netlists, and fixed typos
    [Control Board - Headers.sch, Control Board - Microcontroller IO.sch, Control Board - Microcontroller Power.sch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]
2014-01-07 Fixed error with resistor on JTAG header
    [Control Board - Headers.sch]
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2014-01-28 Moved fuse before power led
    [Control Board - Power.sch]
2014-01-28 Removed extra capacitors C16 and C17
    [Control Board - Microcontroller Power.sch]
2014-01-28 Removed arm IOs, cut down GPIOs to 12 pins
    [Control Board - Microcontroller IO.sch]
2014-01-28 GPIO header reduced to 12 pins
    [Control Board - Peripheral Headers.sch]
2014-01-28 Removed IO lines from arm headers
    [Control Board - Peripheral Headers.sch]
2014-01-28 Moved RF CE pin to pin 31
    [Control Board - Microcontroller IO.sch]
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2014-01-28 Fixed errors, optimized traces, incremented version number
2014-01-29 Replaced pdf with pcb's printout
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2018-03-09 Commit unstaged files for archival purposes
    [Atmel ARM Microcontrollers.csv, Bill of Materials - Control Board.csv, Bill of Materials - Misc Electronics.csv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]
